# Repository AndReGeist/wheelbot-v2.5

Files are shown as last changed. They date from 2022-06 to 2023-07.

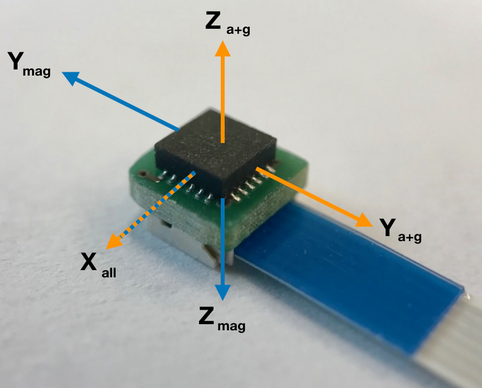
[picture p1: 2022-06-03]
simulation/simulink-model/images/IMU_block_image.PNG

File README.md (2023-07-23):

# wheelbot-v2.5

This repository contains all files required to build a Wheelbot v2.5.

Project page:  [https://sites.google.com/view/wheelbot/start](https://sites.google.com/view/wheelbot/start)

## [/CAD files](https://github.com/AndReGeist/wheelbot-v2.5/tree/main/CAD%20files)
Contains the CAD files of the Wheelbot v2.5 as stl-files.

3D printer used: Markforged Onyx One <br/>
Material: Onyx <br/>
Layer height: 0.2 mm <br/>
Use default settings for all else. <br/>
See the following links for tips on printing: <br/>
https://markforged.com/resources/learn/design-for-additive-manufacturing-plastics-composites/3d-printing-strategies-for-composites/composites-3d-printing-design-tips <br/>
https://static.markforged.com/downloads/CompositesDesignGuide.pdf

The folder also contains the technical drawing for the cut copper rings forming the reaction wheel and the pdf *"wheelbot v2.5 assembly view.pdf"* that lets you interact with the complete Wheelbot's assembly (requires Adobe Acrobate reader).

## [/motherboard circuitry](https://github.com/AndReGeist/wheelbot-v2.5/tree/main/motherboard%20circuitry)
Contains the circuit layouts of the motherboard that connects to the Maevarm M2 and which also supplies the uDriver-v2 with power.

## [/simulation/matlab-symbolic-derivation-EOM](https://github.com/AndReGeist/wheelbot-v2.5/tree/main/simulation/matlab-symbolic-derivation-EOM)
Contains the matlab files used to symbolically derive the EOM of the Wheelbot.

**FlywUni_symbolic_derive.m:** Derives the Euler-Lagrange equations of a unicycle reaction wheel robot using the parameters set in "config_FlyUni" and the "Langrange.m" defined in external libraries.

**FlywUni_symbolic_linearize.m:** Reshapes the symbolic ODE obtained from "FlywUni_symbolic_derive", brings it into the form for the standard matlab ODE solvers and saves it as 
```matlab
save('EQS_matrices_nonlin.mat', 'M_nonlin', 'RHS_nonlin')
```
Also linearizes the set of equations and saves the linearization as 
```matlab
save('EQS_matrices.mat', 'M', 'RHS')
```

**FlywUni_symbolic_analyze.m:** Loads the pre-computed dynamic equations, computes a trajectory using a standard ODE solver (RK45), and plots trajectory and total energy of the system.

## [/simulation/simulink-model](https://github.com/AndReGeist/wheelbot-v2.5/tree/main/simulation/simulink-model)
Contains the simulink model used to tune the estimator and LQR controller. Recommended matlab version is R2020a.

The file *"s00_config"* contains the simulation settings including the exact estimates for the mass and inertia of the Wheelbot v2.5 which we obtained from CAD.

Before running *"s01_unicycle.slx"*, you need to run *"s00_designLQR"*.

## [/firmware](https://github.com/AndReGeist/wheelbot-v2.5/tree/main/firmware)
Contains the firmware required to run Wheelbot v2.5

### /firmware/M2-on-wheelbot
Contains the firmware that runs on a Maevarm M2 that is attached to the motherboard of the Wheelbot.

### /firmware/M2-wifi-dongle
Contains the firmware that runs on a Maevarm M2 being connected to a PC and that handles the wifi communication with the Wheelbot.

### /firmware/computer-python-interface
Python program running on Ubuntu 18.04 LTS collecting incoming data/outgoing commands from/to the wifi dongle.

# Erratum
In the initial publication, in Equation (3), the transform from averaged body rates ${}^{\text{B}}\omega_i$ to Euler rates was incorrectly denoted as

```math
\begin{bmatrix}
\dot{q}_{1, \mathrm{G}} \\
\dot{q}_{2, \mathrm{G}} \\
\dot{q}_{3, \mathrm{G}}
\end{bmatrix} = \begin{bmatrix}
e_1^{\mathrm{T}} R_2 \\
e_2^{\mathrm{T}} \\
e_3^{\mathrm{T}} R_1 R_2
\end{bmatrix} \sum_{k=1}^4 \frac{{ }^B \omega_i(k)}{4},
```

corresponding to

```math
\left[\begin{array}{c}
\dot{q}_{1, \mathrm{G}} \\
\dot{q}_{2, \mathrm{G}} \\
\dot{q}_{3, \mathrm{G}}
\end{array}\right]=\left[\begin{array}{c}
R_2^T e_1 &
e_2 &
R_2^T R_1^T e_3
\end{array}\right]^{\top} \sum_{i=1}^4 \frac{{ }^B \omega_i(k)}{4}.
```

However, the correct transform from averaged body rates ${}^{\text{B}}\omega_i$ to Euler rates is

```math
\left[\begin{array}{c}
\dot{q}_{1, \mathrm{G}} \\
\dot{q}_{2, \mathrm{G}} \\
\dot{q}_{3, \mathrm{G}}
\end{array}\right]=\left[\begin{array}{c}
R_2^T e_1 &
e_2 &
R_2^T R_1^T e_3
\end{array}\right]^{-1} \sum_{i=1}^4 \frac{{ }^B \omega_i(k)}{4}.
```

While we implemented the faulty transform in the Wheelbot's state estimation routine (see [main.c](https://github.com/AndReGeist/wheelbot-v2.5/blob/main/firmware/M2-on-wheelbot/src/main.c), Line 340),  the error had not been noticed during experimentation as the robot remained close to its upright equilibrium. In turn, $q_1$ and $q_2$ remained near zero such that both transforms became almost identical, as

```math
\left[\begin{array}{c}
R_2^T e_1 &
e_2 &
R_2^T R_1^T e_3
\end{array}\right]^{\top} =  \left[\begin{array}{c}
\cos(q_2) & 0 & \sin(q_2) \\
0 & 1 & 0 \\
-\cos(q_1) \sin(q_2) & \sin(q_1) & \cos(q_1) \cos(q_2)
\end{array}\right],
```

```math
\left[\begin{array}{c}
R_2^T e_1 &
e_2 &
R_2^T R_1^T e_3
\end{array}\right]^{-1} = \left[\begin{array}{c}
 \cos(q_2) & 0 & \sin(q_2) \\
 \tan(q_1) \sin(q_2) & 1 & -\tan(q_1) \cos(q_2) \\ 
 -\sin(q_2) / \cos(q_1) & 0 & \cos(q_2) / \cos(q_1)
\end{array}\right].
```

Importantly, **our results on tilt estimation using accelerometers** as depicted in Figure 10 **are not affected by this error**. In the first experiment (Figure 10, left) the robot's tilt angles were kept at zero. In the second experiment (Figure 10, right), $q_1 \approx 0$ such that $\tan(q_1) \approx q_1$. In turn, both transforms deviated only marginally from each other in both experiments.

We added a [Jupyter notebook](https://github.com/AndReGeist/wheelbot-v2.5/blob/main/erratum_bodyrate_transform.ipynb) to the projects Github repository detailing the calculation of the transform from body rates to Euler rates.

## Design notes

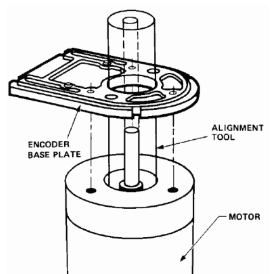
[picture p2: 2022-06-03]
simulation/simulink-model/images/encoder_block_image.PNG

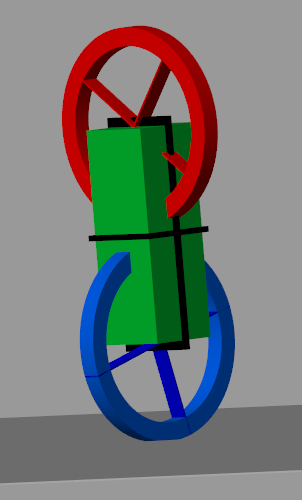
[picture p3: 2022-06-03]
simulation/simulink-model/images/simulation_block_image.PNG

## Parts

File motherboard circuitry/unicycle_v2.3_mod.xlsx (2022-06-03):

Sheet: old
Qty | Value | Device | Parts | LINK_DIGI | LINK_RS | PART_NO_DIGI | PART_NO_MFR | PART_NO_RS | ZWE stock? | count | notes
2 | 21AWG_X2 | 21AWG_X2 | MOTOR-PWR, PWR-CAP |  |  |  |  |  | y
1 | 22-27-2021-02 | 22-27-2021-02 | J1 |  |  |  |  |  | y
1 | ACS780LLRTR-050B-T | ACS780LLRTR-050B-T | CURRENTSENSING |  |  | 620-1817-1-ND | ACS780LLRTR-050B-T |  | n
1 | AP7333AG | AP7333AG | 1V8-REG |  |  |  |  |  | y
1 | ATE1D-2M3-10-Z | ATE1D-2M3-10-Z | SWITCH |  | https://my.rs-online.com/web/p/toggle-switches/0222516/ |  | ATE1D-2M3-10-Z | 222-516 | n
1 | B340LB-13-F | B340LB-13-F | REG-D1 |  | https://de.rs-online.com/web/p/schottky-diodes-rectifiers/9228115/ |  | B340LB-13-F | 922-8115 | n
4 | 100nF | C-EUC0402 | C1, C2, H-CAP2, REG-CBOOT |  |  |  |  |  | y
1 | 10nF | C-EUC0402 | C8 |  |  |  |  |  | y
2 | 1uF | C-EUC0402 | C3, C4 |  |  |  |  |  | y
2 |  | C-EUC0603 | ACS-CBYP, ACS-CF
1 | 10uF | C-EUC0603 | REG-COUT |  |  |  |  |  | y
2 | CSD18540Q5BT | CSD18540Q5BT | MTR-FET, PWR-FET | https://www.digikey.de/product-detail/en/texas-instruments/CSD18540Q5BT/296-37963-1-ND/4915650 |  | 296-37963-1-ND | CSD18540Q5BT |  | y
1 | DF13-5P-1.25DS | DF13-5P-1.25DS | UDRIVER |  |  |  |  |  | y
4 | DF13-6P-1.25DSA | DF13-6P-1.25DSA | IMU-A, IMU-B, IMU-C, IMU-D |  |  |  |  |  | y
1 | 22uH | LHMI-INDUCTOR | REG-L1 |  | https://de.rs-online.com/web/p/multilayer-surface-mount-inductors/7568496/ |  | 74437324220 | 756-8496 | n
1 | LMR16006YQ5DDCRQ1 | LMR16006YQ5DDCRQ1 | 5VREG |  |  | 296-42515-1-ND | LMR16006YQ5DDCRQ1 |  | n
1 | M2 | M2 | U$2 |  |  |  |  |  | y
1 | PMEG045T150EIPD | PMEG045T150EIPD | MTR-DIODE | https://www.digikey.de/product-detail/de/nexperia-usa-inc/PMEG045T150EIPDZ/1727-8328-1-ND/9520869 |  | 1727-8328-1-ND | PMEG045T150EIPD | n/a | n
9 | 1.2k | R-EU_R0402 | CLK-1V8, MOSI-1V8, R9, R13, R14, R15, R18, R19, R21 |  |  |  |  |  | y
2 | 100k | R-EU_R0402 | R31, REG-SHDN |  |  |  |  |  | y
4 | 10k | R-EU_R0402 | R16, R28, R34, REG-R2 |  |  |  |  |  | y
4 | 1k | R-EU_R0402 | R25, R26, R27, R29 |  |  |  |  |  | y
2 | 27k | R-EU_R0402 | R1, R3 |  |  |  |  |  | y
2 | 4.7k | R-EU_R0402 | R2, R4 |  |  |  |  |  | y
1 | 54.9k | R-EU_R0402 | REG-R1 |  |  |  |  |  | y
3 | 620 | R-EU_R0402 | R17, R20, R22 |  |  |  |  |  | y
6 | 680 | R-EU_R0402 | R5, R7, R8, R10, R11, R12 |  |  |  |  |  | y
1 |  | R-EU_R0603 | ACS-RF |  |  |  |  |  | y
1 | 10uF, 45V | TCJD106M050R0120 | REG-CIN | https://www.digikey.com/en/products/detail/avx-corporation/TCJD106M050R0120/2578345 | https://de.rs-online.com/web/p/tantal-elektrolytkondensator/1442463/ | 478-6492-1-ND | TCJD106M050R0120 | 144-2463 | n
1 |  | TPSD337K006R0045 | H-CAP1 | https://www.digikey.com/en/products/detail/avx-corporation/TPSD337K006R0045/929946 | https://de.rs-online.com/web/p/tantal-elektrolytkondensator/1359982/ | 478-3314-1-ND | TPSD337K006R0045 | 135-9982 | n
1 | TXB0101 | TXB0101 | 1V8REG-MISO |  |  |  |  |  | y |  | running low?
1 | VNH7100ASTR | VNH7100ASTR | HBRIDGE |  |  | 497-17629-1-ND | VNH7100ASTR |  | n
2 | XT30PW-M | XT30PW-M | U$8, U$9 |  |  |  |  |  | n

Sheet: -new
Qty | Value | Device | Parts | Description | LINK_DIGI | LINK_RS | PART_NO_DIGI | PART_NO_MFR | PART_NO_RS
2 | 21AWG_X2 | 21AWG_X2 | MOTOR-PWR, PWR-CAP | through hole for 21? AWG wire
1 | 22-27-2021-02 | 22-27-2021-02 | J1 | Molex connector
1 | ACS780LLRTR-050U-T | ACS780LLRTR-050U-T | CURRENTSENSING | Hall Effect Sensor |  |  |  | ACS780LLRTR-050U-T | 146-4456
1 | AP7333AG | AP7333AG | 1V8-REG
1 | ATE1D-2M3-10-Z | ATE1D-2M3-10-Z | SWITCH | Switch | https://www.digikey.com/en/products/detail/nidec-copal-electronics/ATE1D-2M3-10-Z/1792018 | https://my.rs-online.com/web/p/toggle-switches/0222516/ |  | ATE1D-2M3-10-Z | 222-516
1 | B340LB-13-F | B340LB-13-F | REG-D1 | Schottky diode |  | https://de.rs-online.com/web/p/schottky-diodes-rectifiers/9228115/ |  | B340LB-13-F | 922-8115
4 | 100nF | C-EUC0402 | C1, C2, H-CAP2, REG-CBOOT | CAPACITOR, European symbol
1 | 10nF | C-EUC0402 | C8 | CAPACITOR, European symbol
2 | 1uF | C-EUC0402 | C3, C4 | CAPACITOR, European symbol
2 |  | C-EUC0603 | ACS-CBYP, ACS-CF | CAPACITOR, European symbol
1 | 10uF | C-EUC0603 | REG-COUT | CAPACITOR, European symbol
2 | CSD18540Q5BT | CSD18540Q5BT | MTR-FET, PWR-FET | Power MOSFET | https://www.digikey.de/product-detail/en/texas-instruments/CSD18540Q5BT/296-37963-1-ND/4915650 |  | 296-37963-1-ND | CSD18540Q5BT
1 | DF13-5P-1.25DS | DF13-5P-1.25DS | UDRIVER | DF13-5P
4 | DF13-6P-1.25DSA | DF13-6P-1.25DSA | IMU-A, IMU-B, IMU-C, IMU-D | DF13-6P
1 | 22uH | IND-LHMI | REG-L1 | Inductor 22uH |  | https://de.rs-online.com/web/p/multilayer-surface-mount-inductors/7568496/ |  | 74437324220 | 756-8496
1 | LMR16006XDDCT | LMR16006XDDCT | 5VREG | Buck Regulator |  |  | 296-38546-1-ND | LMR16006XDDCT | 914-2986
1 | M2 | M2 | U$2
1 | PMEG045T150EIPD | PMEG045T150EIPD | MTR-DIODE | Diode 45V 15A | https://www.digikey.de/product-detail/de/nexperia-usa-inc/PMEG045T150EIPDZ/1727-8328-1-ND/9520869 |  | 1727-8328-1-ND | PMEG045T150EIPD | n/a
9 | 1.2k | R-EU_R0402 | CLK-1V8, MOSI-1V8, R9, R13, R14, R15, R18, R19, R21 | RESISTOR, European symbol
2 | 100k | R-EU_R0402 | R31, REG-SHDN | RESISTOR, European symbol
4 | 10k | R-EU_R0402 | R16, R28, R34, REG-R2 | RESISTOR, European symbol
4 | 1k | R-EU_R0402 | R25, R26, R27, R29 | RESISTOR, European symbol
2 | 27k | R-EU_R0402 | R1, R3 | RESISTOR, European symbol
2 | 4.7k | R-EU_R0402 | R2, R4 | RESISTOR, European symbol
1 | 54.9k | R-EU_R0402 | REG-R1 | RESISTOR, European symbol
3 | 620 | R-EU_R0402 | R17, R20, R22 | RESISTOR, European symbol
6 | 680 | R-EU_R0402 | R5, R7, R8, R10, R11, R12 | RESISTOR, European symbol
1 |  | R-EU_R0603 | ACS-RF | RESISTOR, European symbol
1 | 10uF, 45V | TCJD106M050R0120 | REG-CIN | Capacitor 10uF 50V | https://www.digikey.com/en/products/detail/avx-corporation/TCJD106M050R0120/2578345 | https://de.rs-online.com/web/p/tantal-elektrolytkondensator/1442463/ | 478-6492-1-ND | TCJD106M050R0120 | 144-2463
1 |  | TPSD337K006R0045 | H-CAP1 | Capacitor 330uF 6.3V | https://www.digikey.com/en/products/detail/avx-corporation/TPSD337K006R0045/929946 | https://de.rs-online.com/web/p/tantal-elektrolytkondensator/1359982/ | 478-3314-1-ND | TPSD337K006R0045 | 135-9982
1 | TXB0101 | TXB0101 | 1V8REG-MISO
1 | VNH7100ASTR | VNH7100ASTR | HBRIDGE | Motor Driver |  |  | 497-17629-1-ND | VNH7100ASTR
2 | XT30PW-M | XT30PW-M | U$8, U$9

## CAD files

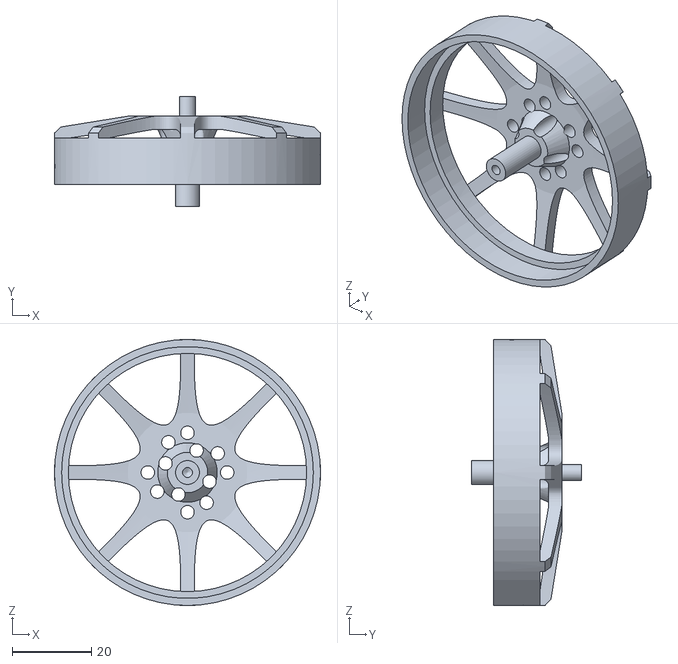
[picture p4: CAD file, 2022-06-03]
CAD files/2DOFRobot_AssmV7 - MotorEncoder_AssmV2.1-2 Flywheel_AssmV2-1 MN6007_Asmbly-1 MN6007_Rotor-2.STL
67.0 x 27.8 x 67.0

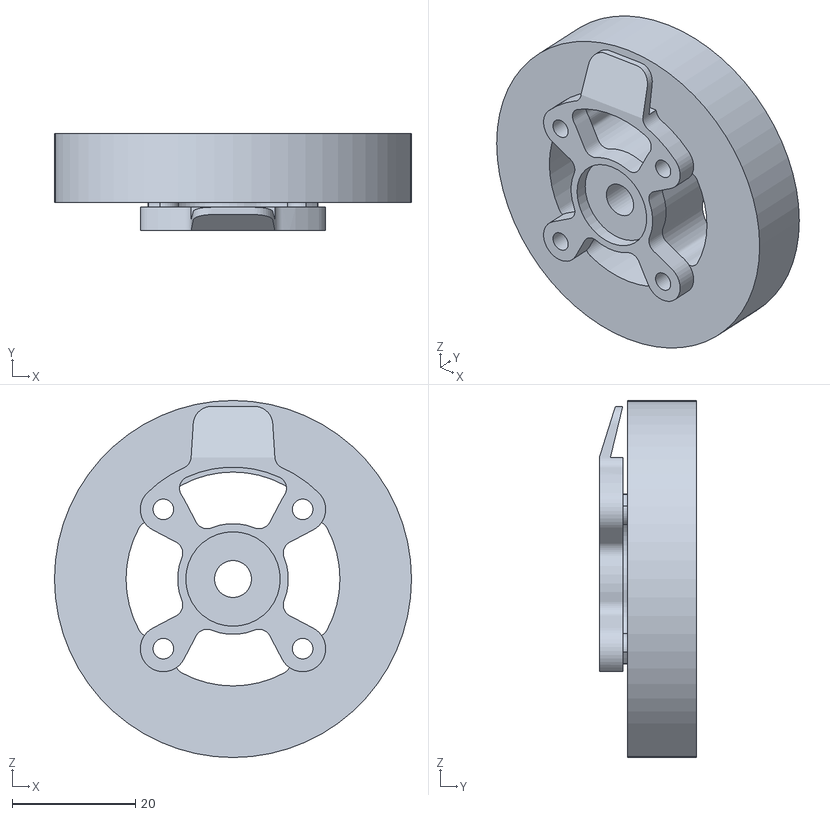
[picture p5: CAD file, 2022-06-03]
CAD files/2DOFRobot_AssmV7 - MotorEncoder_AssmV2.1-2 Flywheel_AssmV2-1 MN6007_Asmbly-1 MN6007_Stator-2.STL
58.0 x 15.8 x 58.0

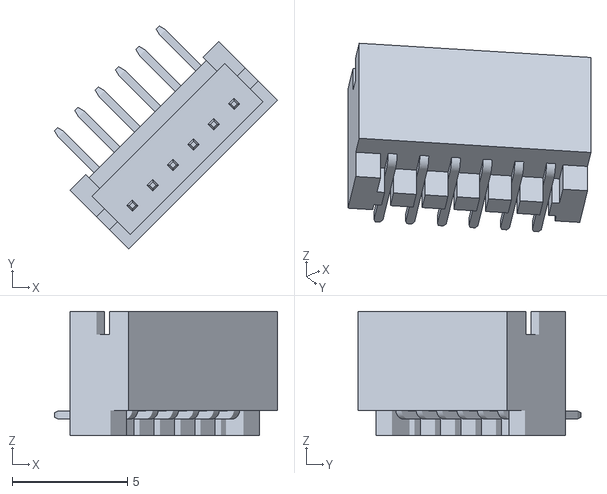
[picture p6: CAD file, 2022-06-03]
CAD files/2DOFRobot_AssmV7 - SS4B-8 DF13-6P-RA-HEADER-1.STL
9.69 x 9.69 x 5.40

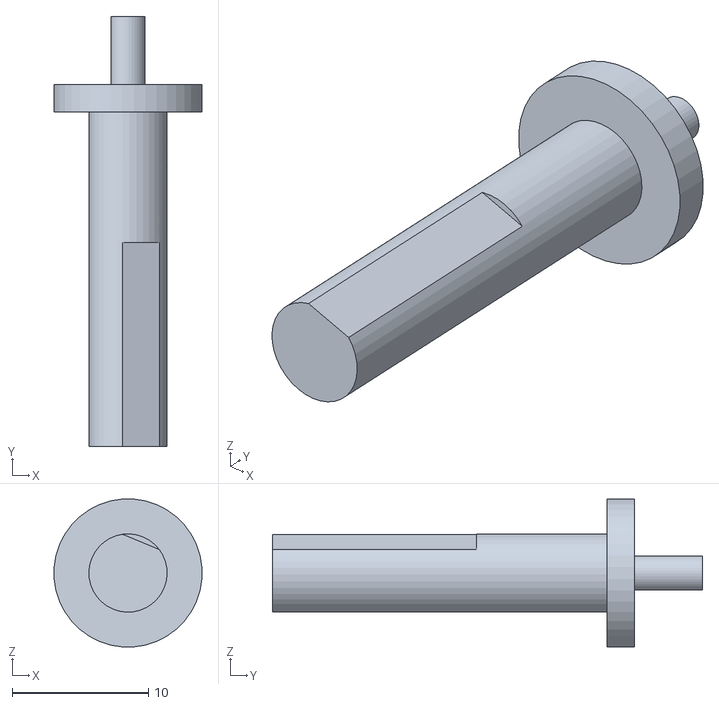
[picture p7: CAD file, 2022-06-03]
CAD files/Machined parts/2DOFRobot_AssmV7 - MotorEncoder_AssmV2.1-2 Flywheel_AssmV2-1 1C3_ShaftV9-Alu-1.STL
10.9 x 31.6 x 10.9

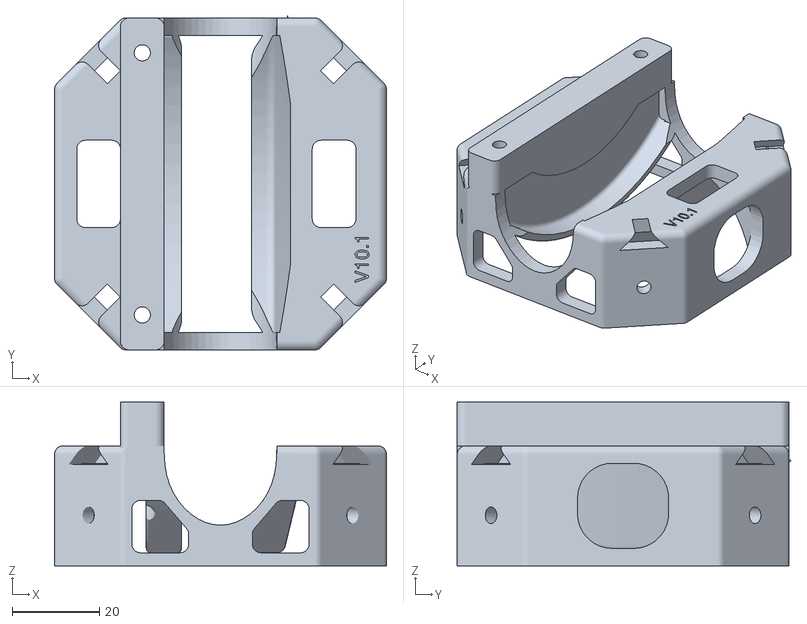
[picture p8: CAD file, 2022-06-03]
CAD files/Markforged 3D prints/2DOFRobot_AssmV7 - 2DOFBodyV10.1-3.STL
76.0 x 76.4 x 37.5

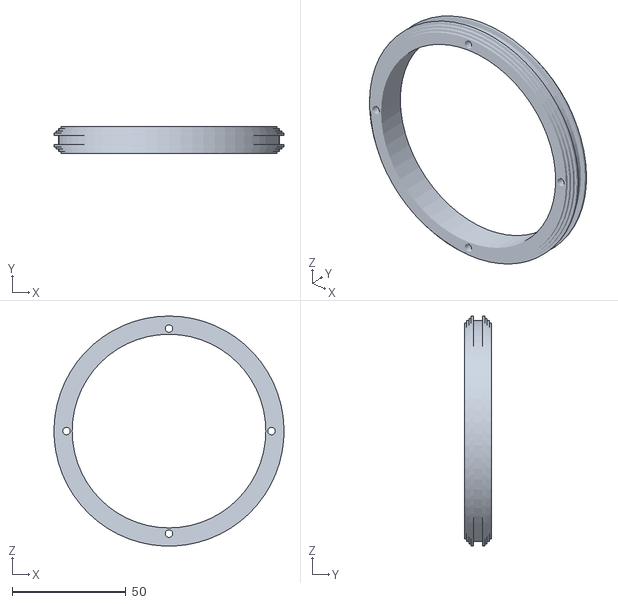
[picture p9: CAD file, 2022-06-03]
CAD files/Machined parts/2DOFRobot_AssmV7 - MotorEncoder_AssmV2.1-2 Flywheel_AssmV2-1 CopperRingBodyV2-1.STL
101.0 x 12.0 x 100.9

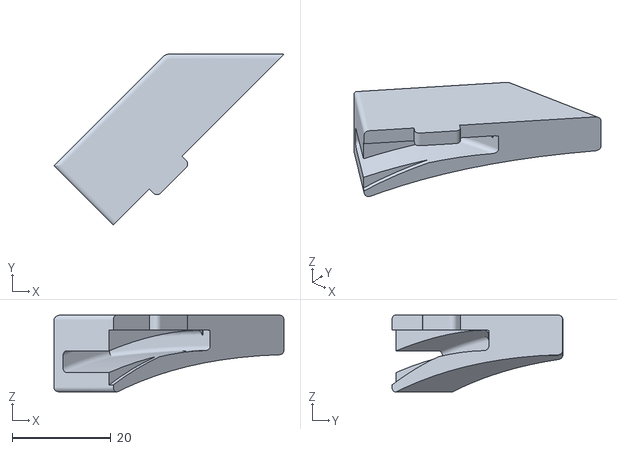
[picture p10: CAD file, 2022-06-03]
CAD files/Markforged 3D prints/2DOFRobot_AssmV7 - bumperAssm-1 sketch v2-L-1.STL
46.6 x 34.6 x 15.6

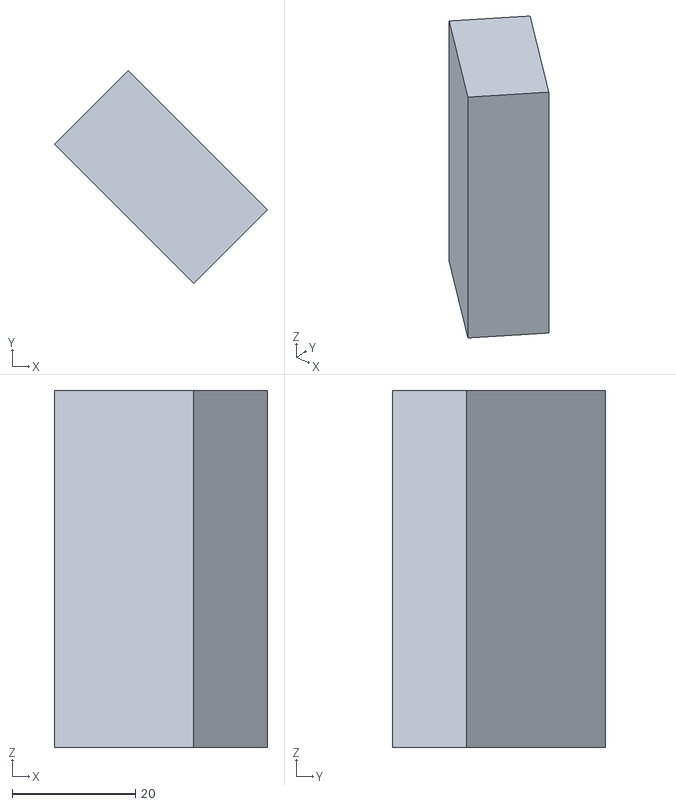
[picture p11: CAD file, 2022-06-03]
CAD files/2DOFRobot_AssmV7 - 6SLipo_31x58x16-1.STL
34.6 x 34.6 x 58.0

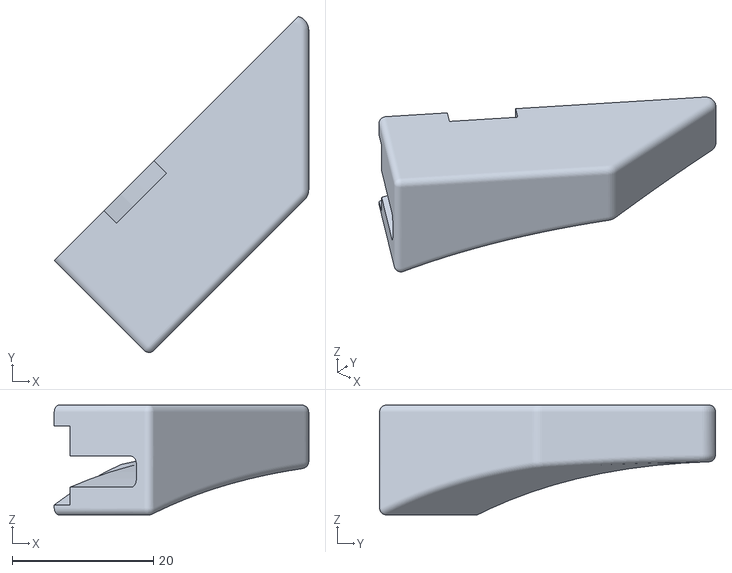
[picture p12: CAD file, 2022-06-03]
CAD files/Markforged 3D prints/2DOFRobot_AssmV7 - bumperAssm-1 sketch v2-R-1.STL
36.1 x 47.6 x 15.6

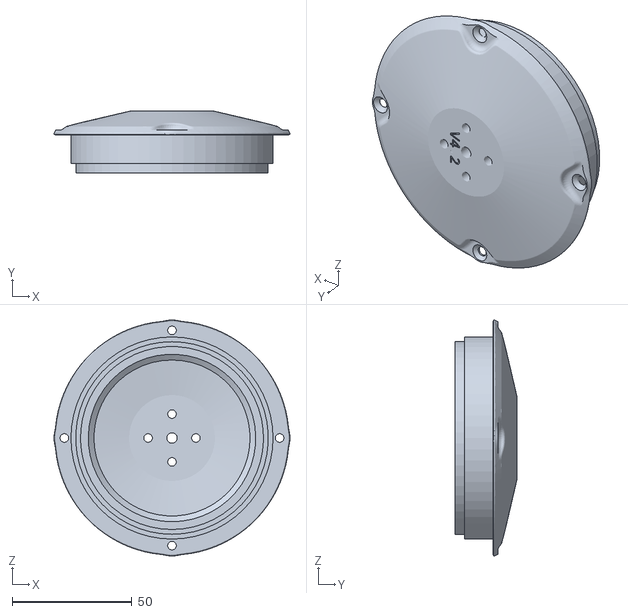
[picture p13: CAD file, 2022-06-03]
CAD files/Markforged 3D prints/2DOFRobot_AssmV7 - MotorEncoder_AssmV2.1-2 Flywheel_AssmV2-1 FlywheelHub_V4.2-1.STL
98.7 x 26.0 x 98.7

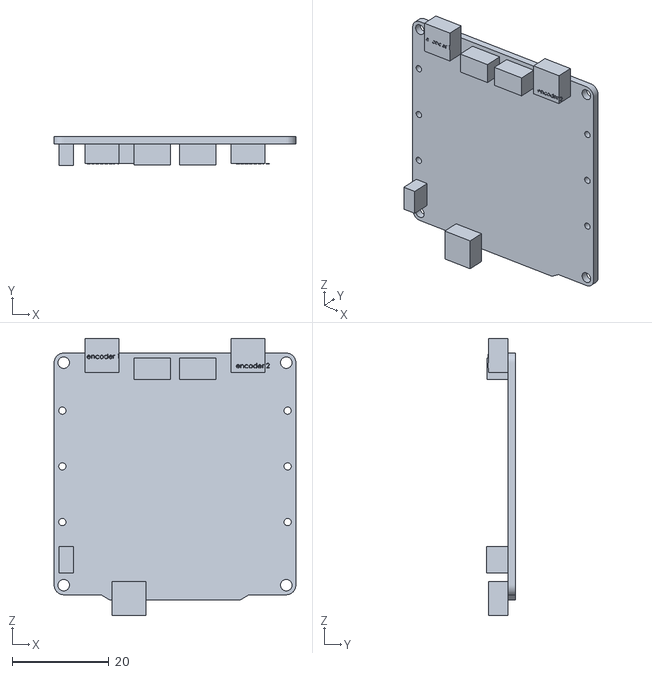
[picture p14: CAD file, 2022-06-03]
CAD files/2DOFRobot_AssmV7 - uDriverV2-1.STL
49.9 x 6.01 x 57.2

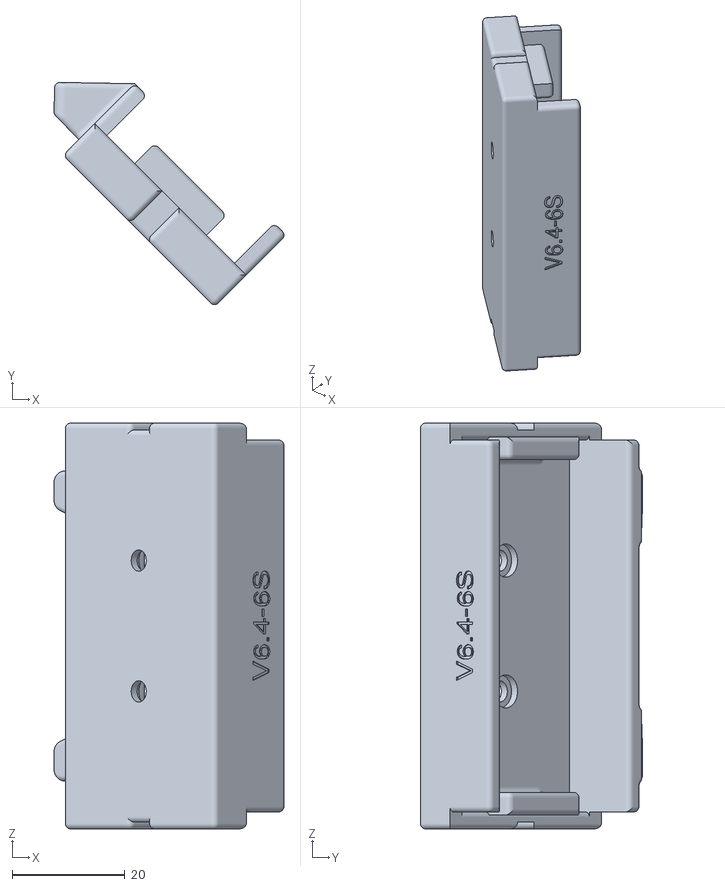
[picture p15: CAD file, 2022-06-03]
CAD files/Markforged 3D prints/2DOFRobot_AssmV7 - batteryCasingV6.4-6S-1.STL
40.8 x 39.4 x 72.0

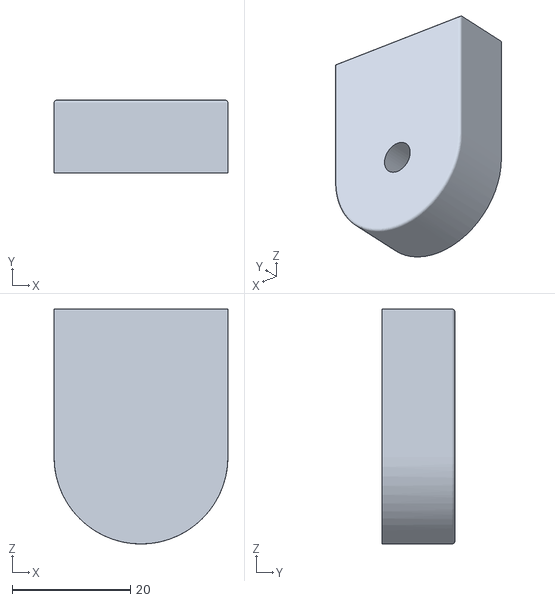
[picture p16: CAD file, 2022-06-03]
CAD files/2DOFRobot_AssmV7 - MotorEncoder_AssmV2.1-2 AEDM5810-1 AEDM5810_Encoder-1.STL
29.4 x 12.3 x 39.7

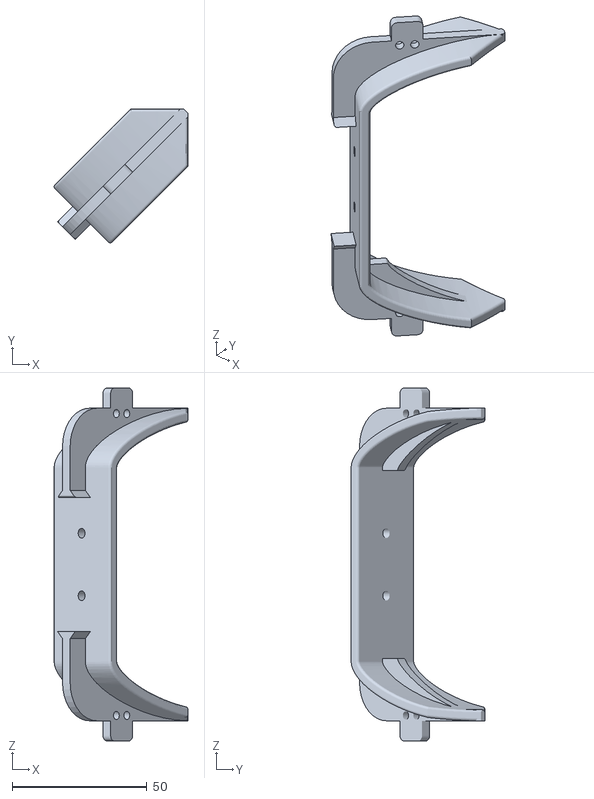
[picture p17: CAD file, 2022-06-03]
CAD files/Markforged 3D prints/2DOFRobot_AssmV7 - bananaV6.3-1.STL
49.6 x 49.6 x 131.0

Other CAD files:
CAD files/2DOFRobot_AssmV7 - SS4B-8 DF13-6P-PLUG-1.STL
CAD files/Markforged 3D prints/2DOFRobot_AssmV7 - MotorEncoder_AssmV2.1-2 MN6007OptEncIntrfV6-1.STL
CAD files/2DOFRobot_AssmV7 - MotorEncoder_AssmV2.1-2 Flywheel_AssmV2-1 ORing95x5-1.STL
CAD files/Markforged 3D prints/2DOFRobot_AssmV7 - MotorEncoder_AssmV2.1-2 Flywheel_AssmV2-1 FlywheelEndringV3.0-1.STL
CAD files/2DOFRobot_AssmV7 - MotorEncoder_AssmV2.1-2 AEDM5810-1 AEDM5810_Cover-1.STL
CAD files/2DOFRobot_AssmV7 - SS4B-8 SS4B_PCB-1.STL
CAD files/screws and inserts/2DOFRobot_AssmV7 - M2 insert-1.STL
CAD files/screws and inserts/2DOFRobot_AssmV7 - M2x8-1.STL
CAD files/screws and inserts/2DOFRobot_AssmV7 - M3 insert with head-1.STL
CAD files/screws and inserts/2DOFRobot_AssmV7 - M3x10-2.STL
CAD files/screws and inserts/2DOFRobot_AssmV7 - MotorEncoder_AssmV2.1-2 Flywheel_AssmV2-1 M3x10-1.STL
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

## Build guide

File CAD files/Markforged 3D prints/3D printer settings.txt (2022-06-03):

3D printer used: Markforged Onyx One
Material: Onyx
Layer height: 0.2 mm
Use default settings for all else.

See the following links for tips on printing:
https://markforged.com/resources/learn/design-for-additive-manufacturing-plastics-composites/3d-printing-strategies-for-composites/composites-3d-printing-design-tips

https://static.markforged.com/downloads/CompositesDesignGuide.pdf

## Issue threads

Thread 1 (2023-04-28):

Empty assembly view

stephane-caron, 2023-04-28:
Thank you for making this awesome open source project :smiley:

This is a quick heads up that the assembly view PDF in ``CAD files/`` is empty.

AndReGeist, 2023-04-30:
Thanks for the heads up! If you open the file with adobe acrobat and click on "Enable multimedia content" then you can see the interactive assembly. Otherwise, the file indeed appears to be empty.

Closed 2023-04-30.

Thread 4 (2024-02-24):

Blank assembly Manual?

MadWayne233, 2024-02-24:
Hello there!
I was looking through the CAD files, trying to make my own Wheelbot, until stumbling upon a blank assembly manual (quite unexpectedly ). It seemed to me that there was nothing more than a blank page. Could you please check if there's anything wrong?

[wheelbot v2.5 assembly view.pdf](https://github.com/AndReGeist/wheelbot-v2.5/blob/main/CAD%20files/wheelbot%20v2.5%20assembly%20view.pdf)

Thanks a lot for your generous OA resources and valuable efforts in recreating a shared and open community!

AndReGeist, 2024-02-25:
Hi MadWayne233,

please try open the file in Adobe Acrobat Reader. Does it work?

MadWayne233, 2024-02-26:
Thanks a lot for your rapid and kind reply :)

I give acrobat a go, but sadly it did not seem to work quite as expected.

MadWayne233
***@***.***

&nbsp;

------------------&nbsp;原始邮件&nbsp;------------------
发件人:                                                                                                                        "AndReGeist/wheelbot-v2.5"                                                                                    ***@***.***&gt;;
发送时间:&nbsp;2024年2月25日(星期天) 晚上11:18
***@***.***&gt;;
***@***.******@***.***&gt;;
主题:&nbsp;Re: [AndReGeist/wheelbot-v2.5] Blank assembly Manual? (Issue #4)

Hi MadWayne233,

please try open the file in Adobe Acrobat Reader. Does it work?

—
Reply to this email directly, view it on GitHub, or unsubscribe.
You are receiving this because you authored the thread.Message ID: ***@***.***&gt;

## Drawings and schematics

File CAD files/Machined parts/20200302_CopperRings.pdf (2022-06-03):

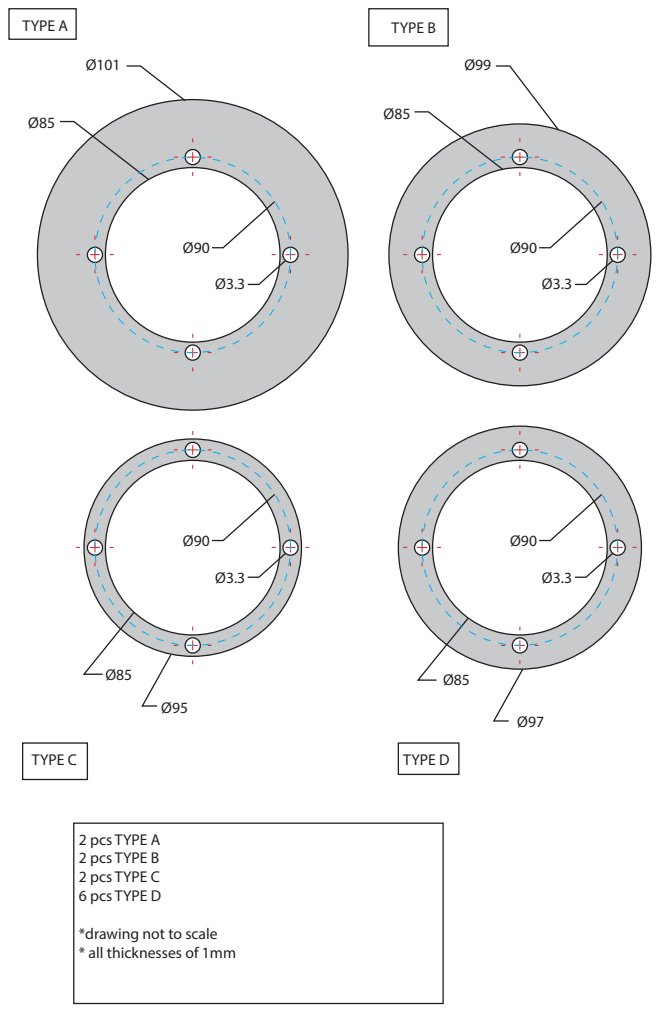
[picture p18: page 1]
TYPE A; TYPE B; TYPE C; TYPE D; 2 pcs TYPE A 2 pcs TYPE B 2 pcs TYPE C 6 pcs TYPE D

*drawing not to scale
* all thicknesses of 1mm

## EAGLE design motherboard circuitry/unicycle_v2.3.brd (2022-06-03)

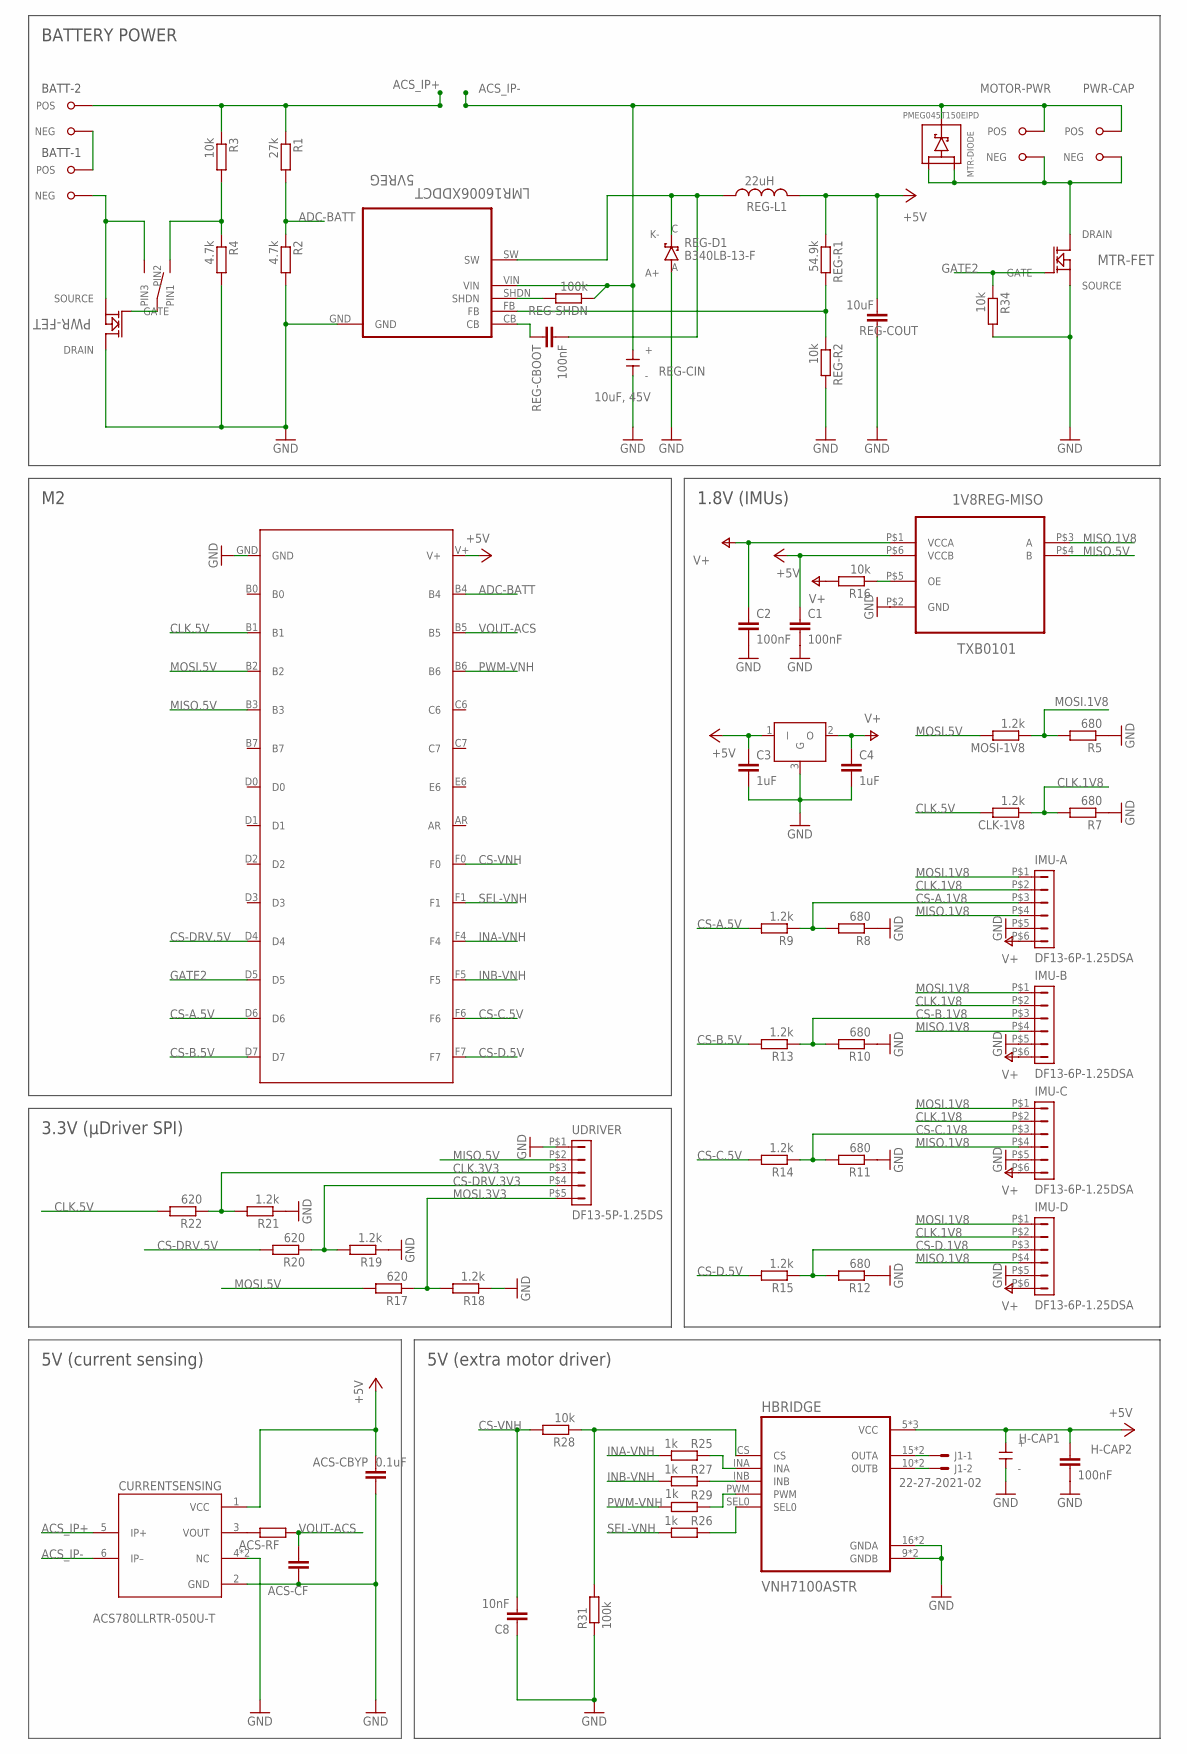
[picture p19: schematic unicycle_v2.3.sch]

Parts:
1V8-REG: AP7333AG; SOT23
1V8REG-MISO: TXB0101; SOT23-6
5VREG: LMR16006XDDCT; SOT95P280X110-6N
ACS-CBYP: 0.1uF; C0603
ACS-CF: C-EUC0603; C0603
ACS-RF: R-EU_R0603; R0603
C1, C2: 100nF; C0402
C3, C4: 1uF; C0402
C8: 10nF; C0402
CLK-1V8: 1.2k; R0402
CURRENTSENSING: ACS780LLRTR-050U-T; XDCR_ACS780LLRTR-050B-T
H-CAP1: TPSD337K006R0045; AVX_TPS-D
H-CAP2: 100nF; C0402
HBRIDGE: VNH7100ASTR; SOIC127P600X175-16N
IMU-A: DF13-6P-1.25DSA
IMU-B: DF13-6P-1.25DSA
IMU-C: DF13-6P-1.25DSA
IMU-D: DF13-6P-1.25DSA
J1: 22-27-2021-02; 6410-02
MOSI-1V8: 1.2k; R0402
MOTOR-PWR: 21AWG_X2
MTR-DIODE: PMEG045T150EIPD
MTR-FET: CSD18540Q5BT; DNK0008A
PWR-CAP: 21AWG_X2
PWR-FET: CSD18540Q5BT; DNK0008A
R1: 27k; R0402
R2, R4: 4.7k; R0402
R3, R16, R28, R34: 10k; R0402
R5, R7, R8, R10, R11, R12: 680; R0402
R9, R13, R14, R15, R18, R19, R21: 1.2k; R0402
R17, R20, R22: 620; R0402
R25, R26, R27, R29: 1k; R0402
R31: 100k; R0402
REG-CBOOT: 100nF; C0402
REG-CIN: 10uF, 45V; TCJD106M050R0120
REG-COUT: 10uF; C0603
REG-D1: B340LB-13-F; DIODES-SMB
REG-L1: 22uH; 4020
REG-R1: 54.9k; R0402
REG-R2: 10k; R0402
REG-SHDN: 100k; R0402
SWITCH: ATE1D-2M3-10-Z
U$2: M2; M1
U$8, U$9: XT30PW-M; XT30PW-M-NOHOLE
UDRIVER: DF13-5P-1.25DS

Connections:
+5V: 1V8-REG.1 (I), 1V8REG-MISO.P$6 (VCCB), ACS-CBYP.2, C1.1, C3.1, CURRENTSENSING.1 (VCC), H-CAP1.POS (+), H-CAP2.1, HBRIDGE.5 (VCC), HBRIDGE.12 (VCC), HBRIDGE.VCC, REG-COUT.1, REG-L1.P$2 (2), REG-R1.1, U$2.V+
ACS_IP+: CURRENTSENSING.5 (IP+), R1.1, R3.1, U$8.POS
ACS_IP-: 5VREG.VIN, CURRENTSENSING.6 (IP–), MOTOR-PWR.POS, MTR-DIODE.3 (K), PWR-CAP.POS, REG-CIN.POS (+), REG-SHDN.1
ADC-BATT: R1.2, R2.1, U$2.B4
CLK.1V8: CLK-1V8.1, IMU-A.P$2 (2), IMU-B.P$2 (2), IMU-C.P$2 (2), IMU-D.P$2 (2), R7.2
CLK.3V3: R21.2, R22.1, UDRIVER.P$3 (3)
CLK.5V: CLK-1V8.2, R22.2, U$2.B1
CS-A.1V8: IMU-A.P$3 (3), R8.2, R9.1
CS-A.5V: R9.2, U$2.D6
CS-B.1V8: IMU-B.P$3 (3), R10.2, R13.1
CS-B.5V: R13.2, U$2.D7
CS-C.1V8: IMU-C.P$3 (3), R11.2, R14.1
CS-C.5V: R14.2, U$2.F6
CS-D.1V8: IMU-D.P$3 (3), R12.2, R15.1
CS-D.5V: R15.2, U$2.F7
CS-DRV.3V3: R19.2, R20.1, UDRIVER.P$4 (4)
CS-DRV.5V: R20.2, U$2.D4
CS-VNH: C8.2, R28.2, U$2.F0
GATE2: MTR-FET.4 (GATE), R34.1, U$2.D5
GND: 1V8-REG.3 (G), 1V8REG-MISO.P$2 (GND), 5VREG.GND, ACS-CBYP.1, ACS-CF.2, C1.2, C2.2, C3.2, C4.2, C8.1, CURRENTSENSING.2 (GND), CURRENTSENSING.4 (NC), CURRENTSENSING.7 (NC), H-CAP1.NEG (-), H-CAP2.2, HBRIDGE.9 (GNDB), HBRIDGE.16 (GNDA), HBRIDGE.GNDA, HBRIDGE.GNDB, IMU-A.P$5 (5), IMU-B.P$5 (5), IMU-C.P$5 (5), IMU-D.P$5 (5), MTR-FET.1 (SOURCE), MTR-FET.2 (SOURCE), MTR-FET.3 (SOURCE), PWR-FET.9 (DRAIN), R2.2, R4.2, R5.1, R7.1, R8.1, R10.1, R11.1, R12.1, R18.1, R19.1, R21.1, R31.1, R34.2, REG-CIN.NEG (-), REG-COUT.2, REG-D1.A (A+), REG-R2.2, U$2.GND, UDRIVER.P$1 (1)
INA-VNH: R25.2, U$2.F4
INB-VNH: R27.2, U$2.F5
MISO.1V8: 1V8REG-MISO.P$3 (A), IMU-A.P$4 (4), IMU-B.P$4 (4), IMU-C.P$4 (4), IMU-D.P$4 (4)
MISO.5V: 1V8REG-MISO.P$4 (B), U$2.B3, UDRIVER.P$2 (2)
MOSI.1V8: IMU-A.P$1 (1), IMU-B.P$1 (1), IMU-C.P$1 (1), IMU-D.P$1 (1), MOSI-1V8.1, R5.2
MOSI.3V3: R17.1, R18.2, UDRIVER.P$5 (5)
MOSI.5V: MOSI-1V8.2, R17.2, U$2.B2
unnamed: 5VREG.SHDN, REG-SHDN.2
unnamed: HBRIDGE.15 (OUTA), HBRIDGE.OUTA, J1.1
unnamed: MOTOR-PWR.NEG, MTR-DIODE.1 (A1), MTR-DIODE.2 (A2), MTR-FET.9 (DRAIN), PWR-CAP.NEG
unnamed: 5VREG.FB, REG-R1.2, REG-R2.1
unnamed: 5VREG.SW, REG-CBOOT.1, REG-D1.C (K-), REG-L1.P$1 (1)
unnamed: 5VREG.CB, REG-CBOOT.2
unnamed: 1V8REG-MISO.P$5 (OE), R16.1
unnamed: U$8.NEG, U$9.POS
unnamed: PWR-FET.1 (SOURCE), PWR-FET.2 (SOURCE), PWR-FET.3 (SOURCE), SWITCH.P$3 (PIN3), U$9.NEG
unnamed: R3.2, R4.1, SWITCH.P$1 (PIN1)
unnamed: HBRIDGE.INB, R27.1
unnamed: HBRIDGE.SEL0, R26.1
unnamed: HBRIDGE.PWM, R29.1
unnamed: PWR-FET.4 (GATE), SWITCH.P$2 (PIN2)
unnamed: HBRIDGE.CS, R28.1, R31.2
unnamed: ACS-RF.2, CURRENTSENSING.3 (VOUT)
unnamed: HBRIDGE.10 (OUTB), HBRIDGE.OUTB, J1.2
unnamed: HBRIDGE.INA, R25.1
PWM-VNH: R29.2, U$2.B6
SEL-VNH: R26.2, U$2.F1
V+: 1V8-REG.2 (O), 1V8REG-MISO.P$1 (VCCA), C2.1, C4.1, IMU-A.P$6 (6), IMU-B.P$6 (6), IMU-C.P$6 (6), IMU-D.P$6 (6), R16.2
VOUT-ACS: ACS-CF.1, ACS-RF.1, U$2.B5

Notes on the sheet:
BATT-1
BATT-2
3.3V (µDriver SPI)
1.8V (IMUs)
BATTERY POWER
5V (extra motor driver)
5V (current sensing)

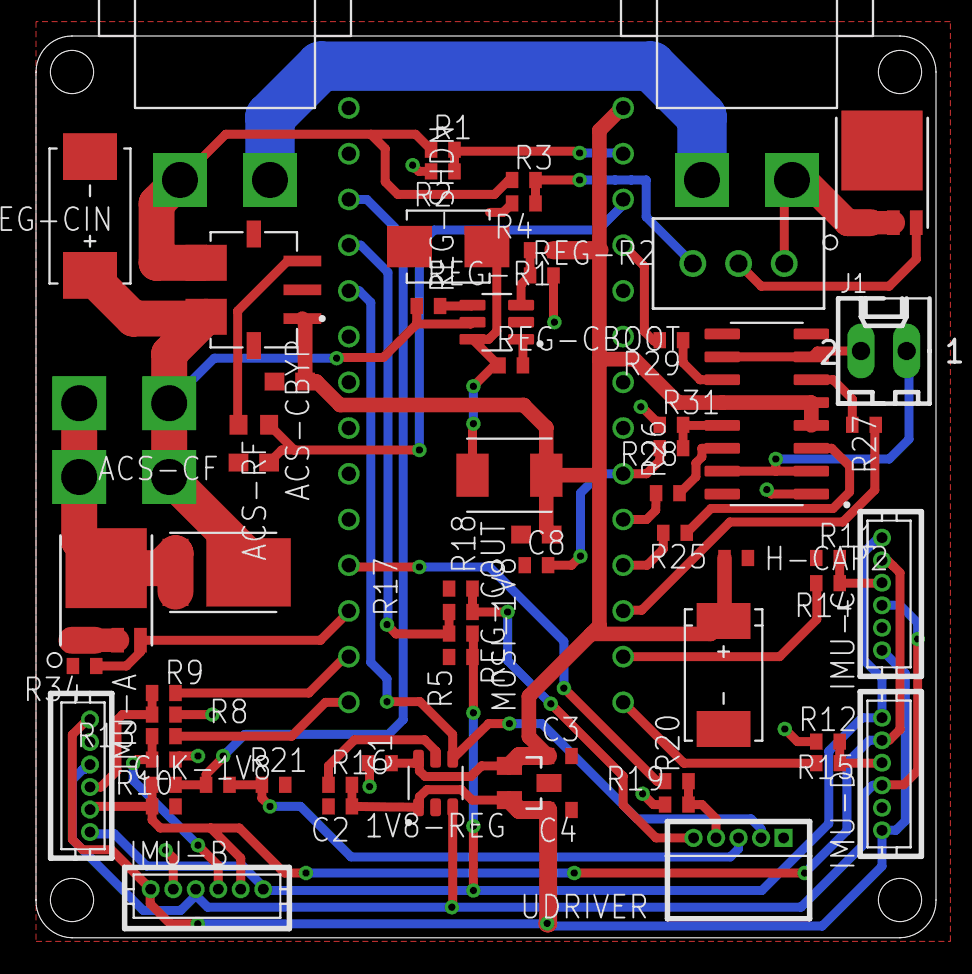
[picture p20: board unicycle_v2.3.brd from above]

Board: 2 copper layers, 50.0 x 50.1 mm, 68 parts (0 on the bottom side), 49 nets.

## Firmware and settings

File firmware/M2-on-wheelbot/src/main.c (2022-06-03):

/**************************************************************************
 *
 *  Header Files to include
 *
 **************************************************************************/
/* subystem header files */
#include "control.h"
#include "icm20948.h"
#include "m_bus.h"
#include "m_rf.h"
#include "m_spi.h"
#include "m_usb.h"
#include "matrix_calculations.h"
#include "state_estimation.h"
#include "udriver.h"
#include "checks.h"

/* global program files */
#include "config.h"
#include "m_general.h"

/* External header files */
#include <avr/wdt.h> // Watchdog
#include <string.h> // Used in check_crc

/**************************************************************************
 *
 *  Function declarations
 *
 **************************************************************************/
void init(); // prototype the initialization function
void setup_timer();
uint16_t select_timer1_prescaler();
uint16_t micros( bool stream );
void init_calibrate_udriver();
bool check_crc( uint8_t *data_in_ptr );
void data_write( uint8_t *packet, int index, float scaling, float data );
void read_usb( uint8_t *buffer );

 /**************************************************************************
 *
 *  Global Variables - these are the only non-stack RAM usage
 *
 **************************************************************************/
volatile bool tick = FALSE; // ISR tick when loop is executed
volatile bool new_data = FALSE; // ISR tick when wifi data_out is being received
uint16_t counter = 0;  // counter used to count control loops
uint16_t counter_lastwifi = 0;  // Last loop that wifi signal has been received
volatile uint8_t cycle_overflow_counter = 0;
Commstruct comm_ud; // Change scope to main and why volatile??

bool stream = TRUE;                                             // Start streaming input
bool transmitOK;

/**************************************************************************
 *
 *  Main function
 *
 **************************************************************************/
int main() {
	/* Error messages are stored in sys_flag
	 * 0: All good
	 * 1: Encoder 1 not properly initialized
	 * 2: Encoder 2 not properly initialized
	 * 3: Loop execution time is too long, check TICK (> 0.01 seconds)
	 * 4: Loop did not fully execute
	 * 5: Loop execution time is almost too long (>0.08 seconds)
	 * 6: Estimator calibration has been triggered
	 */
	uint16_t sys_flag = 0;
	float max_rate_motor2 = 50.0;  // Max rate in rad/s, 400 RPM

	/*
	 * usb_control: If TRUE, USB connection is used instead of RF
	 * use_IMUS: If FALSE, no IMU readings are obtained and control is switched off
	 */
	FlagsStruct flags = { .system = TRUE, .wifi = TRUE, .angle = TRUE, .rate = TRUE, .control = TRUE, .battery = TRUE,
						  .upright = FALSE, .standup1 = FALSE, .standup1_done = FALSE, .standup2 = FALSE,
						  .standup2_done = FALSE, .bias = FALSE , .loop_finished = TRUE, .LQRcontrol1 = FALSE, .LQRcontrol2 = FALSE,
						  .useLQR1 = FALSE, .useLQR2 = FALSE, .do_standup = FALSE, .do_rollup = FALSE,
						  .usb_control = FALSE, .use_IMUs = TRUE, .motor_test = FALSE,
						  .use_pivotAcc_CP = TRUE, .use_pivotAcc_WC_vel = FALSE, .use_pivotAcc_WC_acc = FALSE};

	uint16_t battery_voltage;
	uint16_t tick_time = 0; // Check time between ticks
	uint16_t loop_time = 0; // Check time of control loop

	float time_test_start = 0.0; // Variable used in function "test_motor" to store start time of motor test

	////////////////////////////////////////
	// uDRIVER - MOTOR CONTROL VARIABLES
	////////////////////////////////////////
	Commstruct comm_ud = { .currentLimit1=0.0, .currentTargetMotor1=0.0, .currentLimit2=0.0, .currentTargetMotor2=0.0,
						   .currentMotor1=0.0, .positionMotor1=0.0, .velocityMotor1=0.0, .currentMotor2=0.0,
						   .positionMotor2=0.0, .velocityMotor2=0.0, .status_errcode=0, .status_SE=FALSE, .status_M1E=FALSE,
						   .status_M1R=FALSE, .status_IDX1D=FALSE, .status_IDX1T=FALSE, .status_M2E=FALSE, .status_M2R=FALSE,
						   .status_IDX2D=FALSE, .status_IDX2T=FALSE };

	////////////////////////////////////////
	// IMU VARIABLES
	////////////////////////////////////////
	a_range_t acc_range = ACCEL_2G;
	g_range_t gyro_range = GYRO_500DPS;  //g_range_t gyro_range = GYRO_2000DPS;
	float accel_scaling = 0.000598755; // ACCEL_2G transforms bit in m/s2  //float accel_scaling = 0.00119751; // ACCEL_4G
	float gyro_scaling = 0.0002663161;  // Transform bit to max 500°/s in rad/s

	m2_gpio_t imu_list[NUM_SENSORS] = {IMU_A, IMU_B, IMU_C, IMU_D}; // Chip select pins for each sensor
	float IMUx[NUM_SENSORS] = {-PI/2, -PI/2, PI/2, PI/2};
	float IMUz[NUM_SENSORS] = {(-3*PI)/4, PI/4, -PI/4, (3*PI)/4};
	int32_t R_b_IMU[3][3] = {{0.0}};

	int16_t accel_adjust[NUM_SENSORS][3] = {0}; // bias adjust for accel
	int16_t imu_acc[3] = {0};
	//int16_t imu_acc_C[3] = {0};
	int32_t imu_acc_tmp[3] = {0};

	int16_t imu_gyro[3] = {0};
	int32_t imu_gyro_tmp[3] = {0};

	int16_t imu_data[NUM_SENSORS][NUM_IMU_DATA] = {0}; // data in the body frame

	float body_rate[NUM_DIM] = {0}; // Gyroscope body rate estimate in body frame
	//float euler_rate[NUM_DIM] = {0}; // Gyroscope body rate estimate as Euler rates DELETE

	////////////////////////////////////////
	// VARIABLES FOR ESTIMATOR
	////////////////////////////////////////
	float roll_bias = 0.07; //0.05; //0,0043 // -0.0124; //-0.02; //0.0; //0.00331; //0.00874; //-0.04; //-0.03; //-0.0416; //-0.005; //-0.01; //-0.048; //0.026;
	float pitch_bias = 0.00;//0.017; //-0.0523; //−0,0863//0.0173; //-0.05; //-0.05; //-0.037; //-0.04; //-0.062; //-0.031;

	float roll_bias_sum = 0.0;
	float pitch_bias_sum = 0.0;

	float q[5] = {INIT_ANGLE, 0.0, 0.0, 0.0, 0.0};  // Initial Roll and Pitch angle
	float q_acc[2] = {INIT_ANGLE, 0.0};  // Attitude est. from accelerometer measurements, set to zero before calibration
    float q_acc_nopivot[2] = {INIT_ANGLE, 0.0}; // DEBUG - DELETE
	float dq[5] = {INIT_ANGLE, 0.0, 0.0, 0.0, 0.0};  // Initial Roll and Pitch angle
	float dq4_prev = 0.0;

	float ddq4_est = 0.0;
	float acc_pivot_B[3] = {0.0, 0.0, 0.0};
	float acc_pivot_B0[3] = {0.0, 0.0, 0.0}; // DEBUG - DELETE
	float T[3][3] = {0};                                        // Transformation matrix from body rate to euler rate
	T[0][0] = cos(q[1]);
	T[0][1] = 0.0;
	T[0][2] = sin(q[1]);
	T[1][0] = 0.0;
	T[1][1] = 1;
	T[1][2] = 0;
	T[2][0] = -cos(q[0])*sin(q[1]);
	T[2][1] = sin(q[0]);
	T[2][2] = cos(q[0])*cos(q[1]);

	int16_t acc_ref0[NUM_SENSORS][NUM_DIM] = {0}; // Array to store reference acceleration in IMU frames to get bias in calibration
	uint16_t counter_tmp = 0;
	uint16_t counts = 0;
	counter_ptr = count_start;

	////////////////////////////////////////
	// VARIABLES FOR WIFI
	////////////////////////////////////////
	uint8_t data_in[PACKET_LENGTH_IN] = {0}; // data coming from PC
	uint8_t data_in_prev[PACKET_LENGTH_IN] = {0}; // data coming from PC
	uint8_t data_out[PACKET_LENGTH] = {0}; // data sent to PC
	uint8_t data_in0 = 0;

	uint32_t *crc_out_ptr = (uint32_t *)&data_out[28];
	bool crc_in_OK = TRUE;

	float scaling_attitude = 32767.0 / PI;
	float scaling_current = 32767.0 / 40;
	float scaling_rate = (32767.0 / 3000) * (60 / (2 * PI)); // Motorrate is measured in rad/s, max rate 3000 RPM
	float init_q5_est = 0.0;
	float init_q4_est = 0.0;

	uint16_t durations[5] = {0};
	float controls[5] = {0.0};
	float* motor_ptr;
	bool* flag_ptr;
	uint16_t ramp_length1 = 0;
	uint16_t ramp_length2 = 5;


	// ***************************************
	// ININITILIZATION
	// ***************************************
	init();

	// UDRIVER INIT
	init_calibrate_udriver(&comm_ud); // initialize and calibrate BLDC motor

	if ( flags.use_IMUs == TRUE ){

		start1: // initialize each IMU with same settings
		for ( int i = 0; i < NUM_SENSORS; ++i ) {
			if ( icm20948_init( imu_list[i], acc_range, gyro_range ) ) {
				m_green( ON );
				m_wait( INIT_WAIT );
				m_green( OFF );
			} else {
				m_red( TOGGLE );
				m_wait( 5 * INIT_WAIT );
				goto start1;
			}
		} // end for

		// SPI speed reset, somehow IMU init. takes different SPI_MHZ (?)
		m_spi_speed(SPI_4MHZ);
		//m_spi_speed(SPI_1MHZ);
		//m_spi_speed(SPI_500KHZ);
		//m_spi_speed( SPI_125KHZ );

		// measure accelerometer bias. can be stored in hardware for the future
		acc_ref0[0][0] = 5793;  // x, initial acceleration in IMU frame taken from simulation
		acc_ref0[0][1] = -14189; // y, Note that 1g = 16384
		acc_ref0[0][2] = 5793;  // z

		acc_ref0[1][0] = -5793;   // x
		acc_ref0[1][1] = -14189; // y
		acc_ref0[1][2] = -5793; // z

		acc_ref0[2][0] = 5793; // x
		acc_ref0[2][1] = 14189; // y
		acc_ref0[2][2] = 5793; // z

		acc_ref0[3][0] = -5793;  // x
		acc_ref0[3][1] = 14189; // y
		acc_ref0[3][2] = -5793;  // z

		icm20948_calib_accel(&imu_list[0], &accel_adjust[0][0], acc_ref0[0]);
		icm20948_calib_accel(&imu_list[1], &accel_adjust[1][0], acc_ref0[1]);
		icm20948_calib_accel(&imu_list[2], &accel_adjust[2][0], acc_ref0[2]);
		icm20948_calib_accel(&imu_list[3], &accel_adjust[3][0], acc_ref0[3]);
		 } // end if

	start2: // wait until python interface sends "Start wheelbot" signal
	if (data_in[0] == 'i') {
		m_green( ON );
	} else {

		if (flags.usb_control == TRUE) {
			if( m_usb_rx_available() )
			{
				read_usb( &data_in[0] );
	        }
			data_out[PACKET_LENGTH-2] = 0;
			data_out[PACKET_LENGTH-1] = 0; // If !crc_2PC_OK set 'crc2' to 1
			m_usb_tx_char('X');
			usb_serial_write(data_out, PACKET_LENGTH);
		}
		else
		{
			if ( new_data == TRUE )
			{
				new_data = FALSE;
				m_rf_read( (char *) data_in, PACKET_LENGTH_IN );
				check_crc( data_in );
			}
			*crc_out_ptr = m_crc32( (uint8_t *)data_out, 28 );
			m_rf_send( TXADDRESS, (char *) data_out, PACKET_LENGTH );
		}

		m_green( TOGGLE );
		m_red( TOGGLE );
		m_wait( INIT_WAIT );
		goto start2;
	}

  tick_time = micros(FALSE);
  m_red( OFF ); // phew, we made it
  m_green( OFF );

  // ******************************************************************************
  //
  // WHILE-LOOP
  //
  // ******************************************************************************

  while (1) {

	if (tick) {
	  tick_time = micros(FALSE);
	  ++counter;
	  tick = FALSE;
	  check_tick_time(&flags, &sys_flag, &tick_time);


      // ***************************************
	  // GET MOTOR RATES
	  // ***************************************
	  dq[3] = 0.3 * comm_ud.velocityMotor2 + 0.7 * dq[3]; // LOWER WHEEL
	  dq[4] = 0.3 * comm_ud.velocityMotor1 + 0.7 * dq[4]; // UPPER WHEEL

	  q[3] += (dq[3] / (float)LOOP_FREQ); // Integrate rates
	  q[4] += (dq[4] / (float)LOOP_FREQ);

	  //ddq4_est = 0.9 * (dq[3] - dq4_prev) * LOOP_FREQ + 0.1 * ddq4_est; // LP filter derivative of dq[3]
	  //ddq4_est = (dq[3] - dq4_prev) * LOOP_FREQ; // Derivative of dq[3]
	  //dq4_prev = dq[3];
	  //ddq4_est = 0.8 * (comm_ud.velocityMotor2 - dq4_prev) * LOOP_FREQ + 0.2 * ddq4_est; // LP filter derivative of dq_4
	  ddq4_est = (comm_ud.velocityMotor2 - dq4_prev) * LOOP_FREQ; // Derivative of dq_4
	  dq4_prev = comm_ud.velocityMotor2;

	  if ( flags.use_IMUs == TRUE )
	  {

		// ***************************************
		// GET IMU data, REMOVE ACC BIAS, TRANSFORM TO BODY-FIXED FRAME
		// ***************************************
		for (int i = 0;  i < NUM_SENSORS; ++i) {
			icm20948_get_raw_6dof(imu_list[i], imu_acc, imu_gyro);

			for (int j = 0;  j < 3; ++j) {
				imu_acc[j] -= accel_adjust[i][j];
			}

			rot_b_IMU(R_b_IMU, IMUx[i], IMUz[i]); // Compute body-frame transform scaled by 10000
		    multiply_matrix_vector_long(3, 3, R_b_IMU, imu_acc, imu_acc_tmp);
		    multiply_matrix_vector_long(3, 3, R_b_IMU, imu_gyro, imu_gyro_tmp);

			for (int j = 0;  j < 3; ++j) {
				imu_data[i][j] = (int)( imu_acc_tmp[j] / 10000 ); // the entries of rot_b_IMU are scaled by 10000
				imu_data[i][j+3] = (int)( imu_gyro_tmp[j] / 10000 );
			}
		}

		body_rate[0] =
		    (float)( imu_data[0][3] * 0.25 + imu_data[1][3] * 0.25 + imu_data[2][3] * 0.25 + imu_data[3][3] * 0.25 ) * gyro_scaling; // x
		body_rate[1] =
		    (float)( imu_data[0][4] * 0.25 + imu_data[1][4] * 0.25 + imu_data[2][4] * 0.25 + imu_data[3][4] * 0.25 ) * gyro_scaling; // y
		body_rate[2] =
		    (float)( imu_data[0][5] * 0.25 + imu_data[1][5] * 0.25 + imu_data[2][5] * 0.25 + imu_data[3][5] * 0.25) * gyro_scaling; // z


		// ***************************************
		// TRANSFORM BODY RATE TO EULER RATES
		// ***************************************
		// Transformation matrix from body rate to Euler rate
		// Note: Euler rate defined here as [Roll, Pitch, Yaw]
		T[0][0] = cos(q[1]);
		T[0][1] = 0.0;
		T[0][2] = sin(q[1]);
		T[1][0] = 0.0;
		T[1][1] = 1;
		T[1][2] = 0;
		T[2][0] = -cos(q[0])*sin(q[1]);
		T[2][1] = sin(q[0]);
		T[2][2] = cos(q[0])*cos(q[1]);

		multiply_matrix_vector(3, 3, T, body_rate, dq);


		// ***************************************
		// GET ATTITUDE ESTIMATE FROM GYRO
		// ***************************************
		q[0] += (dq[0] / LOOP_FREQ);
		q[1] += (dq[1] / LOOP_FREQ);


		// ***************************************
		// ESTIMATE STATE
		// ***************************************
		estimate_pivot_acc_linearized(acc_pivot_B, q, dq, ddq4_est, &flags);  // Compute acc_pivot_B
		attitude_estimate_accel(q_acc,  acc_pivot_B, &imu_data[0][0]); // Compute q_acc

		//attitude_estimate_accel(q_acc_nopivot,  acc_pivot_B0, &imu_data[0][0]);

		q[0] = FUSION_TUNING_PARAMETER * q_acc[0] + (1 - FUSION_TUNING_PARAMETER) * q[0] ;
		q[1] = FUSION_TUNING_PARAMETER * q_acc[1] + (1 - FUSION_TUNING_PARAMETER) * q[1] ;

	  } // end if


      // ***************************************
      // EXECUTE COMMAND e.g. compute control
      // ***************************************

	  // LQR CONTROL
	  if ( data_in[0] == 'C' )
	  {
			  flags.useLQR1 = TRUE;
			  flags.useLQR2 = TRUE;
	  }
	  // Two-step standup
	  else if ( data_in[0] == 'S' || data_in[0] == 's')
	  {
        flags.do_standup = TRUE;
		motor_ptr = &comm_ud.currentTargetMotor1;

		if ( data_in[0] == 's' ) { flags.standup1_done = TRUE; }

		if ( !flags.standup1_done && ( fabs(q[0]) > 0.072 ) && (comm_ud.velocityMotor1 < 220) )
		{
				flag_ptr = &flags.standup1_done;
				durations[0] = 1; durations[1] = 100; durations[2] =120; durations[3] = 150; durations[4] = 0;
				controls[0] = 0.0; controls[1] = -5.0; controls[2] = -0.0; controls[3] = 15.56; controls[4] = 0;
		}
		else if ( !flags.standup2_done )
		{
				if (flags.standup2 = FALSE)
				{
					flags.standup2 = TRUE;
					flags.standup1_done = TRUE;
					counter_ptr = count_start; // Resets count function
					counts = 0; // Resets counts just to be sure
				}
				ramp_length2 = 10;
				flag_ptr = &flags.standup2_done;
				durations[0] = 150; durations[1] = 250; durations[2] = 310; durations[3] = 340; durations[4] = 0;
				controls[0] = 0.0; controls[1] = -5.0;  controls[2] = -0.5; controls[3] = 14.53; controls[4] = 0;

				if (q[0] < 0.1 && counts > 250) { flags.standup2_done = TRUE; flags.useLQR1 = TRUE; }
				if (fabs(q[0]) < 0.3 && counts > 250) { flags.useLQR2 = TRUE; }
		}
		else
		{
				flags.do_standup = FALSE;
				flags.standup2_done = TRUE;
				flags.useLQR1 = TRUE;
				flags.useLQR2 = TRUE;
		}
	  }
      // Two-step roll-up
	  else if ( data_in[0] == 'U' || data_in[0] == 'u')
	  {
        flags.do_standup = TRUE;
		motor_ptr = &comm_ud.currentTargetMotor2;

		if ( data_in[0] == 'u' ) { flags.standup1_done = TRUE; }

		if ( !flags.standup1_done || comm_ud.velocityMotor2 > 270 )
		{
				ramp_length2 = 10;
				max_rate_motor2 = MAX_RATE_MOTOR1;
				flag_ptr = &flags.standup1_done;
				durations[0] = 1; durations[1] = 100; durations[2] = 120; durations[3] =155; durations[4] = 195;
				controls[0] = 0.0; controls[1] = -5.0, controls[2] = 0.0; controls[3] = 14.93; controls[4] = -5.6;
		}
		else if ( !flags.standup2_done )
		{
				if (flags.standup2 = FALSE)
				{
					flags.standup2 = TRUE;
					flags.standup1_done = TRUE;
					counter_ptr = count_start; // Resets count function
					counts = 0; // Resets counts just to be sure
					max_rate_motor2 = 50;
				}
				ramp_length2 = 4;
				flag_ptr = &flags.standup2_done;
				durations[0] = 1; durations[1] = 2; durations[2] = 3;  durations[3] = 350;  durations[4] = 360;
				controls[0] = 0.0;  controls[2] = 0.0; controls[2] = 0.0;  controls[3] = 0.0;  durations[4] = 6.0;

				if (fabs(q[1]) < 0.3 && counts > 250) { flags.useLQR1 = TRUE; }
				if (fabs(q[1]) < 0.05 && counts > 250) { flags.standup2_done = TRUE; flags.useLQR2 = TRUE; }
		}
		else
		{
				max_rate_motor2 = 50;
				flags.do_standup = FALSE;
				flags.standup2_done = TRUE;
				flags.useLQR1 = TRUE;
				flags.useLQR2 = TRUE;
		}
	  }
      // CALIBRATE ESTIMATOR
      else if (data_in[0] == 'A')
      {
		  sys_flag = 6;
		  flags.useLQR1 = TRUE;
		  flags.useLQR2 = TRUE;

		  // Estimate bias
		  compute_estimator_bias(&flags, counter, &counter_tmp, &roll_bias, &roll_bias_sum,
								 &pitch_bias, &pitch_bias_sum, q );
	  }
	  // SIMPLE MOTOR COMMANDS
	  else if (data_in[0] == 'M')
	  {
		      comm_ud.currentTargetMotor1 = 1.0;
		      comm_ud.currentTargetMotor2 = 0.0;
	  }
	  else if (data_in[0] == 'm') {
		    comm_ud.currentTargetMotor1 = -1.0;
		    comm_ud.currentTargetMotor2 = 0.0;
	  }
	  else if (data_in[0] == 'T') {
		    comm_ud.currentTargetMotor1 = 0.0;
		    comm_ud.currentTargetMotor2 = 1.0;
	  }
	  else if (data_in[0] == 't') {
		    comm_ud.currentTargetMotor1 = 0.0;
		    comm_ud.currentTargetMotor2 = -1.0;
	  }
	  else if (data_in[0] == 'K') {
			comm_ud.currentTargetMotor1 = 1.5 * test_motor(&flags, counter, &time_test_start); 	// TEST MOTOR CONTROL
	  }

    // JUMP
    if ( flags.do_standup ) { feedforward_signal(motor_ptr, flag_ptr, &counter, &counter_tmp, &counts, durations, controls, ramp_length1, ramp_length2); }

	// ROLL CONTROLLER
	if (flags.useLQR1)
	{
		if (flags.LQRcontrol1 == FALSE) { flags.LQRcontrol1 = TRUE; init_q5_est = q[4]; }
		comm_ud.currentTargetMotor1 = return_current_roll(q[0]-roll_bias, dq[0], q[4] - init_q5_est, dq[4]);
	}

	// PITCH CONTROLLER
	if (flags.useLQR2)
	{
		if (flags.LQRcontrol2 == FALSE) { flags.LQRcontrol2 = TRUE; init_q4_est = q[3]; }
		comm_ud.currentTargetMotor2 = return_current_pitch(q[1]-pitch_bias, dq[1], q[3] - init_q4_est, dq[3]);
	}

	// ***************************************
	// CHECK SAFETY AND SEND CONTROL
	// ***************************************
	//reset_checks(&flags, &comm_ud, &data_in[0]);
	check_control(&flags, &comm_ud);
	check_rates(&flags, &comm_ud, max_rate_motor2);
	//check_battery(&flags, &battery_voltage);
	check_upright(&flags, &comm_ud, q);

	if ( flags.usb_control ){ check_wifi(&flags, counter, counter_lastwifi); }

	flags.system = flags.system && flags.wifi && flags.angle && flags.rate && flags.control && flags.battery;

	if (!flags.system || data_in[0] == 'e')
	{
	  comm_ud.currentTargetMotor1 = 0.0;
	  comm_ud.currentTargetMotor2 = 0.0;
	  send_spi_udriver(&comm_ud);
	  m_red( ON );
	}
	else if (flags.system)
	{
	  send_spi_udriver(&comm_ud); // Send current to motor
	}


	// ***************************************
	// USB / WIFI COMMUNICATION
	// ***************************************
	#if DATA_MODE == 1 // GET DATA FOR CONTROL PLOTS
		data_write(data_out, 0, scaling_attitude, q[0] - roll_bias);  // roll, q[0] - roll_bias, q_acc[0]
		data_write(data_out, 2, scaling_attitude, q[1] - pitch_bias);  // pitch, q[1] - pitch_bias, q_acc[1]
		data_write(data_out, 4, 1/gyro_scaling, dq[0]); // roll_rate
		data_write(data_out, 6, 1/gyro_scaling, dq[1]); // pitch_rate
		data_write(data_out, 8, scaling_current, comm_ud.currentTargetMotor1); // motor 1 current sent
		data_write(data_out, 10, scaling_current, comm_ud.currentTargetMotor2); // motor 2 current sent
		data_write(data_out, 12, scaling_rate, dq[4]); // motor 1 rate - comm_ud.velocityMotor1
		data_write(data_out, 14, scaling_rate, dq[3]); // motor 2 rate - comm_ud.velocityMotor2

		#if FLAG_PLOT == 1 // MISC
		  data_write(data_out, 16, scaling_current, comm_ud.currentTargetMotor2); // DEBUG 1
		  data_write(data_out, 18, 32767/200.0, acc_pivot_B[0]); // DEBUG 2
		  data_write(data_out, 20, scaling_rate, dq4_prev); // DEBUG 3
		#endif

		#if FLAG_PLOT == 2 // SYS FLAG + MOTOR POS
		  data_write(data_out, 16, 1.0, sys_flag); // DEBUG 1
		  data_write(data_out, 18, 32767.0 / (10000*PI), q[4] - init_q5_est); // DEBUG 2
		  data_write(data_out, 20, 32767.0 / (10000*PI), q[3] - init_q4_est); // DEBUG 3
		#endif

		#if FLAG_PLOT == 3
		  data_write(data_out, 16, 1.0, sys_flag); // DEBUG 1
		  data_write(data_out, 18, 0.5, loop_time); // DEBUG 2
		  data_write(data_out, 20, 0.5, tick_time); // DEBUG 3
		#endif

		#if FLAG_PLOT == 6 // PIVOT ACC
		  data_write(data_out, 16, 32767/200.0, acc_pivot_B[0]); // DEBUG 1
		  data_write(data_out, 18, scaling_rate, comm_ud.velocityMotor1); // DEBUG 2
		  data_write(data_out, 20, scaling_current, comm_ud.currentTargetMotor2); // DEBUG 3
		#endif

		#if FLAG_PLOT == 7  // ESTIMATOR BIAS
		  data_write(data_out, 16, 1.0, sys_flag); // DEBUG 1
		  data_write(data_out, 18, 32767/1.8, roll_bias); // DEBUG 2
		  data_write(data_out, 20, 32767/1.8, pitch_bias); // DEBUG 3
		#endif

		#if FLAG_PLOT == 8  // DATA IN
		  data_write(data_out, 16, 1.0, data_in[0]); // DEBUG 1
		  data_write(data_out, 18, 1.0, data_in[1]); // DEBUG 2
		  data_write(data_out, 20, 1.0, data_in[9]); // DEBUG 3
		#endif

		#if FLAG_PLOT == 9 // DATA IN
		  data_write(data_out, 16, 1.0, sys_flag); // DEBUG 1
		  data_write(data_out, 18, scaling_current, comm_ud.currentMotor1); // DEBUG 2
		  data_write(data_out, 20, scaling_current, comm_ud.currentMotor2); // DEBUG 3
		#endif

		#if FLAG_PLOT == 10 // DATA IN
		  data_write(data_out, 16, 1/gyro_scaling, dq[2]); // DEBUG 1
		  data_write(data_out, 18, scaling_attitude, q_acc[0]); // DEBUG 2
		  data_write(data_out, 20, scaling_attitude, q_acc[1]); // DEBUG 3
		#endif
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

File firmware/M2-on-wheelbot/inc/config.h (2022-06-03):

#ifndef IMUTEST_CONFIG
#define IMUTEST_CONFIG
/**************************************************************************
 *
 *  SETTINGS
 *
 **************************************************************************/
#define INIT_WAIT 100  // ms to wait after init. each IMU
#define LOOP_FREQ 100  // desired polling freq [Hz] of IMUs
#define TIME_STEP (1/LOOP_FREQ)  // desired polling freq [Hz] of IMUs
#define CALIB_NUM_SAMPLES 20 // amount of samples used for calibrating gyro + accelerometer.
#define NUM_SENSORS 4           // number of sensors
#define NUM_DIM 3
#define NUM_IMU_DATA 6

/* MOTHERBOARD PIN ASSIGNMENT
 * 0: Motherboard as used on Wheelbot v2
 * 3: New motherboard as designed by Naomi and detailed in Confluence
 */

#define PCB_VERSION 0

#if PCB_VERSION == 3
		#define IMU_A PIN_D6         // pin of IMU 1 (closest to hinge)
		#define IMU_B PIN_D7         // pin of IMU 2 (furthest to hinge)
		#define IMU_C PIN_F6
		#define IMU_D PIN_F7
		#define BATTERY_VOLTAGE PIN_B4 // 34V max, 5V ADC max, 1bit=23.5mV
		#define MIN_BATTERY_VOLTAGE 22.4 * 30.09
		#define MD PIN_D4  // uDriver CS pin
		//#define MP PIN_D5  // Power switch to udriver
#endif

#if PCB_VERSION == 0
		#define IMU_A PIN_D6         // pin of IMU 1 (closest to hinge)
		#define IMU_B PIN_D7         // pin of IMU 2 (furthest to hinge)
		#define IMU_C PIN_D3
		#define IMU_D PIN_D4
		#define BATTERY_VOLTAGE PIN_FO // 34V max, 5V ADC max, 1bit=23.5mV
		#define MIN_BATTERY_VOLTAGE 22.4 * 28.0
		#define MD PIN_D5  // uDriver CS pin
#endif

#define MOTOR_KV 160.0 // kv of motor
#define MOTOR_V 24.5 // nominal voltage of motor
#define MOTOR_TORQUE_CONSTANT 0.075 //0.06//0.075 //0.09375//(0.050259456) // kt of motor
#define FUSION_TUNING_PARAMETER 0.02 // tuning parameter for complementary filter


#define NOPE 3000 // Treshold at which gyro values are discarded
#define NOPE2 52 // Treshold at which gyro values are discarded

// ranges for gyro and accel
//#define accel_r ACCEL_2G
//#define gyro_r GYRO_500DPS

// filters for gyro and accel
//#define accel_f ACC_LPF_5HZ
//#define gyro_f GY_LPF_41HZ

#define MAX_CURRENT_MOTOR 20.0 // Max current in Amps, the MN6007 KV160 has a max. peak current of 18A
#define MAX_CURRENT_LQR 15.0
#define MAX_RATE_MOTOR1 330.0  // Max rate in rad/s, 3150 RPM
// The max. motor rate of the MN6007 Kv160 is 3800 RPM
// 398 rad/s = 3800 RPM
// 314 rad/s = 3000 RPM
// 210 rad/s = 2000 RPM
// 10 rad/s = 95 RPM
#define INIT_ANGLE -0.524 //-0.524
#define Rw 0.049 // Wheel radius used for pivot point acc. computation

#define DATA_MODE 1

/* DATA_MODE
 * 1: CONTROL PLOTS -> FLAG_CONTROL = ?
 * 2: PIVOT ACC PLOTS
 * 3: IMU acc
 * 4: IMU rate
 * */

/* FLAG_PLOT chooses which additional data to send to PC
 *  1: MISC
 *  2: sys_flag, q[4] - init_q5_est, q[3] - init_q4_est
 *  3: sys_flag, loop_time,
 *  6: acc_pivot_B[0], comm_ud.velocityMotor2, comm_ud.currentTargetMotor2
 *  7: sys_flag, roll_bias, pitch_bias
 *  8: data_in[0], data
 *  9: sys_flag, comm_ud.currentMotor1, comm_ud.currentMotor2
 *  10: dq[2], q_acc[0], q_acc[1]
 *  11: acc_pivot_B[0], acc_pivot_B[1], acc_pivot_B[2]
 *  12:
 *  13: imu_data[3][0], acc_pivot_B[0], comm_ud.velocityMotor2
 */

#define FLAG_PLOT 9 // 9

/**************************************************************************
 *
 *  Constants
 *
 **************************************************************************/
#define F_CPU 16000000 // freq of CPU
#define GRAV 9.81
#define PI 3.14159265358979
#define PI_2 1.57079632679 // pi/2
#define STATIC_INIT_VALUE 70000
#define MD_PACKET_SIZE 34

// Setup wifi comm
#define CHANNEL 1
#define RXADDRESS 0xF4
#define TXADDRESS 0x54
#define PACKET_LENGTH 32
#define PACKET_LENGTH_IN 32 // Note that m_rf_open() requires PACKET_LENGTH = PACKET_LENGTH_IN

#endif // IMUTEST_CONFIG_H

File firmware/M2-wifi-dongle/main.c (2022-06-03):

#include "m_general.h"
#include "m_usb.h"
#include "m_bus.h"
#include "m_rf.h"
#include "m_crc32.h"

#define CHANNEL 1
#define RXADDRESS 0x54
#define TXADDRESS 0xF4
#define PACKET_LENGTH_2PC 32
#define PACKET_LENGTH_2WB 32

bool check_crc( uint8_t *data_in_ptr );
void read_usb( uint8_t *buffer );

volatile bool new_data;
uint8_t data_2PC[PACKET_LENGTH_2PC] = {0}; // Wifi data coming FROM Wheelbot
uint8_t data_2WB[PACKET_LENGTH_2WB] = {0}; // Wifi data send TO wheelbot
uint32_t *crc_2WB_ptr  = (uint32_t *)&data_2WB[PACKET_LENGTH_2WB-4];
bool crc_2PC_OK;

uint16_t counter = 0;  // counter used to count control loops


int main(void)
{
    // INITIALIZE
	m_red(ON);                                  // use the red LED to verify that we complete initialization
	m_clockdivide(0);                           // 16 Mhz
	m_disableJTAG();                            // access to F port pins
	m_rf_open(CHANNEL, RXADDRESS, PACKET_LENGTH_2PC); // enable mRF
	m_usb_init();                               // enable USB
	while(!m_usb_isconnected());                // wait for USB enumeration
    
    //for(i=0;i<PACKET_LENGTH_2PC;i++){               // send an all-zero data_2WB to PC
    //    m_usb_tx_hex8(data_2PC[i]);
    //}
	m_usb_tx_char('X');
	usb_serial_write( data_2PC, PACKET_LENGTH_2PC );
    m_red(OFF);
    
	while(1){
		++counter;

		if( m_usb_rx_available() )
		{
			read_usb( &data_2WB[0] );
		}

        if( new_data ){
			new_data = FALSE;

			// RECEIVE DATA FROM WHEELBOT
			m_rf_read( (char *) data_2PC, PACKET_LENGTH_2PC );
			//if ( (counter % 100)==0 ){ data_2PC[4] = 'J'; } // DEBUG - Test CRC
			crc_2PC_OK = check_crc( data_2PC );

			/* CODE FOR DEBUGING CRC
			data_2PC[16] = crc_2PC[0]; data_2PC[17] = crc_2PC[1];
			data_2PC[18] = crc_2PC[2]; data_2PC[19] = crc_2PC[3];
			*/
			//data_2PC[21] = crc_2PC_OK; // DEBUG 3
			//data_2PC[20] = 0;
			//crc_2PC_OK = TRUE;

			if( crc_2PC_OK )
			{
				data_2PC[PACKET_LENGTH_2PC-2] = 0;
				data_2PC[PACKET_LENGTH_2PC-1] = 0;
			}
			else if( !crc_2PC_OK ) // If !crc_2PC_OK set 'crc2' to 1
			{
				data_2PC[PACKET_LENGTH_2PC-2] = 1;
				data_2PC[PACKET_LENGTH_2PC-1] = 0;
			}
			m_usb_tx_char('X');
			usb_serial_write( data_2PC, PACKET_LENGTH_2PC );
			m_green( TOGGLE ); // Flash green if wifi data is coming in


			// SEND DATA TO WHEELBOT
			m_wait(0.1);
			*crc_2WB_ptr  = m_crc32((uint8_t *)data_2WB, PACKET_LENGTH_2WB-4);
			m_rf_send(TXADDRESS, (char *) data_2WB, PACKET_LENGTH_2WB);
			m_red( TOGGLE ); // Flash red if wifi data is going out
        } // endif newdata
	} // close while
}  // close main

ISR(INT2_vect){                                 // thrown on new-data_2WB receipt
    new_data = TRUE;
}

bool check_crc( uint8_t *data_2PC_ptr )
{ // Check crc of incoming message
	uint8_t crc_2PC[4] = {0};
	uint32_t *crc_2PC_ptr = (uint32_t *)&crc_2PC[0];

	*crc_2PC_ptr = m_crc32( data_2PC_ptr, PACKET_LENGTH_2PC-4 );

	bool crc_OK;
	crc_OK = (( crc_2PC[0] == data_2PC_ptr[PACKET_LENGTH_2PC-4] )
			  && ( crc_2PC[1] == data_2PC_ptr[PACKET_LENGTH_2PC-3] )
			  && ( crc_2PC[2] == data_2PC_ptr[PACKET_LENGTH_2PC-2] )
			  && ( crc_2PC[3] == data_2PC_ptr[PACKET_LENGTH_2PC-1] ));

	return crc_OK;
}

void read_usb(uint8_t *buffer) { // Reads in chars if the first char is an 'X'
		if(m_usb_rx_char() == 'X')	// new packet incoming!
		{
			int i;
			for(i=0; i < PACKET_LENGTH_2WB; i++)
			{
				while(!m_usb_rx_available());	// wait for byte
				buffer[i] = m_usb_rx_char();
			}
		}
}

void data_write(char *packet, int index, float scaling, float data) {

	int temp = 0;

	temp = (int)(scaling * data);
	packet[index] = *(((char *)&temp) + 1);
	packet[index+1] = *(char *)&temp;
}

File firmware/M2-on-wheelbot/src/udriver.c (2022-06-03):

#include "udriver.h"
/*
 * Script: udriver.c
 * -----------------
 *  variable initialization and functions for SPI communication with uDriver
 *
 *  Info:
 *
 */

/**************************************************************************
 *
 *  Variables
 *
 **************************************************************************/

uint8_t mosi[MD_PACKET_SIZE] = {0};
uint8_t miso[MD_PACKET_SIZE] = {0};

uint16_t desiredMode = 0;
uint8_t crc_check[4] = {0};
uint32_t *crc_check_ptr = (uint32_t *)&crc_check[0];
bool crcOK;
uint16_t boardStatus;
uint16_t communicationInputIndex;
//uint16_t timestamp;

// MOSI POINTERS
uint16_t *mode = (uint16_t *)&mosi[0];
//int32_t *refPosition1 = (int32_t *)&mosi[2];
//int32_t* refPosition2 = (int32_t*)&mosi[6];
// int16_t *refVelocity1 = (int16_t *)&mosi[10]; // DEBUG: Commented out as not needed for current control
// int16_t* refVelocity2 = (int16_t*)&mosi[12]; // DEBUG: Commented out as not needed for current control
int16_t *refCurrent1 = (int16_t *)&mosi[14];
int16_t* refCurrent2 = (int16_t*)&mosi[16];
//uint16_t* kp1 = (uint16_t*)&mosi[18];
//uint16_t* kp2 = (uint16_t*)&mosi[20];
//uint16_t* kd1 = (uint16_t*)&mosi[22];
//uint16_t* kd2 = (uint16_t*)&mosi[24];
uint8_t *currentSaturation1 = (uint8_t *)&mosi[26];
uint8_t *currentSaturation2 = (uint8_t*)&mosi[27];
uint16_t *sendIdx = (uint16_t *)&mosi[28];
uint32_t *sendCrc = (uint32_t *)&mosi[30];

// MISO POINTERS
uint16_t *status = (uint16_t *)&miso[0];
uint16_t *ts = (uint16_t *)&miso[2];
int32_t *mPositionMotor1 = (int32_t *)&miso[4];
int32_t *mPositionMotor2 = (int32_t*)&miso[8];
int16_t *mVelocityMotor1 = (int16_t *)&miso[12];
int16_t *mVelocityMotor2 = (int16_t*)&miso[14];
int16_t *mcurrentMotor1 = (int16_t *)&miso[16];
int16_t *mcurrentMotor2 = (int16_t*)&miso[18];
uint16_t *r_a = (uint16_t *)&miso[20];
uint16_t *r_b = (uint16_t *)&miso[22];
//uint16_t *mADCMotor1 = (uint16_t *)&miso[24];
//uint16_t *mADCMotor2 = (uint16_t*)&miso[26];
uint16_t *receiveIndex = (uint16_t *)&miso[28];
uint32_t *receiveCrc = (uint32_t *)&miso[30];

/**************************************************************************
 *
 *
 *  Functions
 *
 **************************************************************************/
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

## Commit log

2022-06-03 Added motherboard circuit layouts
    [unicycle_v2.3.brd, unicycle_v2.3.sch, unicycle_v2.3_mod.xlsx]
2022-06-03 Added CAD files (stl format) of wheelbot v2.5
    [2DOFRobot_AssmV7 - 2DOFBodyV10.1-3.STL, 2DOFRobot_AssmV7 - 6SLipo_31x58x16-1.STL, 2DOFRobot_AssmV7 - M2 insert-1.STL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]
2022-06-03 Added pdf file of assembled robot
